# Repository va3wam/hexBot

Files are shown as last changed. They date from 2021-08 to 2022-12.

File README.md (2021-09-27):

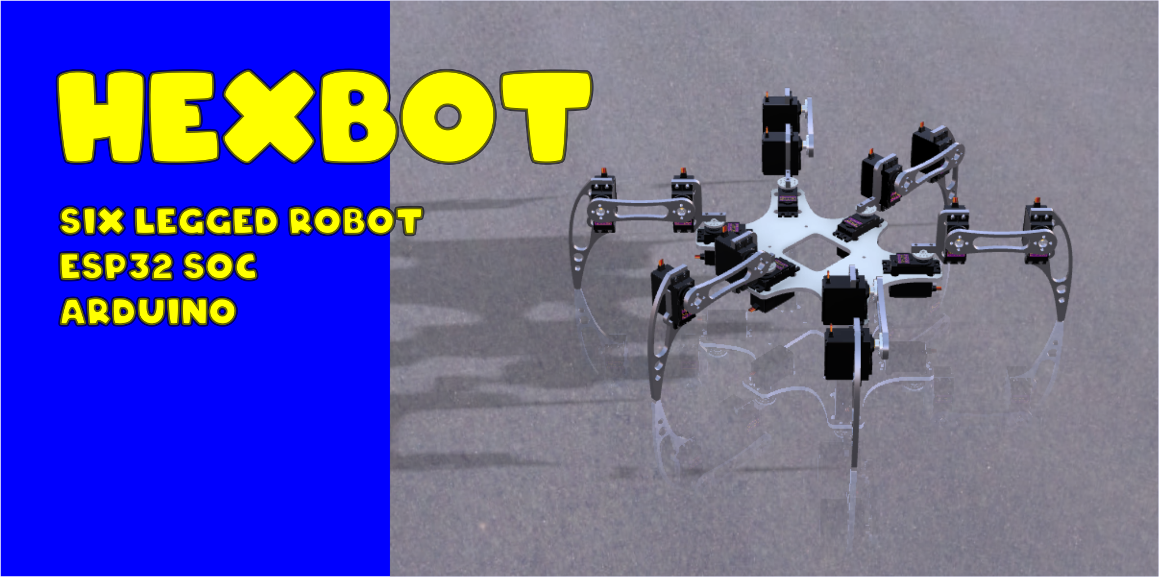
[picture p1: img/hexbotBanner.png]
hexaBot




This repository contains the Arduino source code that runs on an embedded processor at the heart of the six legged robot we call HexBot. The goals of this project can be found [here](goals.md). 

# Getting Started

This project requires that you have a Hexbot robot. The Robot is made up of a custom robot chassis and PCB as well as the code in this repository. Without a version 3 or later Hexbot robot this code will not be very useful to you. 

# Documentation

Here is an index of links to helpful documents found in this repository.

## Constructing a Hexbot Robot
* List of [hardware components](/docs/hexbotHardware.md).
* Hexbot [assembly instructions](/docs/hexbotAssembly.md).
* How to [wire the motors](/docs/wireMotors.md).

## Hexbot User Guides
* Hexbot's [Web interface](/docs/hexbotWebInterface.md).
* How to [configure NVRAM remotely](/docs/hexbotWebInterface.md#config-updater-screen).
* How to [perform OTA updates](/docs/hexbotWebInterface.md#ota-updater-screen).
* Available [MQTT commands](/docs/mqttCommands.md).
* [Hexbot Operations manual](/docs/hexbotOperationManual.md).

## Hexbot Developers Guide

### Prerequisites

In order to make use of the code in this repository you will require the following items.

* A Hexbot robot made up of [this hardware](/docs/hexbotHardware.md).
* The [Hexbot custom PCB](/docs/hexbotCircuit.md).
* An [MQTT broker](/docs/MQTTbroker.md) used by the robot's [MQTT web interface](/docs/hexbotWebInterface.md).  
* A [clone](/docs/cloneRepository.md) of the Hexbot gitHub repository into your own local Git repository.

### Development Software Stack

* How to [clone](/docs/cloneRepository.md) the Hexbot gitHub repository.
* Sample [platformio.ini](AA/platformIO-MAC-example.txt) template.
* Set up [PlatformIO](https://github.com/va3wam/hexBot/blob/main/docs/cloneRepository.md#set-up-platformio).
* Recommended Visual Studio Code [plugins](https://github.com/va3wam/hexBot/blob/main/docs/cloneRepository.md#visual-studio-code-plugins).

### Code Compatability

Hexbot software runs as a monolithic firmware image. The high level logic and peripheral interactions are handled using Arduino C++. FreeRTOS is used to run a WiFi stack as well as the primitive xTaskCreatePinnedToCore() which is used to manage mutli-threaded process execution.

Hexbot's firmware is intended to run on the Espressif ESP WROOM32 "Software On a Chip" (SOC). The development board used for this SOC is the [Zerynth DOIT Esp32 DevKit v1](https://testzdoc.zerynth.com/reference/boards/doit_esp32/docs/). ```We may be switching to a different board``` Note that some standard Arduino functions such as AnalogWrite() have not been implemented on the ESP32 SOC and alternate functions such as ledcSetup(), ledcAttachPin() and ledcWrite() must be used in their place. There are some additional compatability issues of note as follows:

* The GPIO pin usage is loosey Adafruit featherboard compliant meaning it will work with some boards such as the Adafruit OLED featherboard.
* This code will NOT run on an ESP8266 unmodified because of both GPIO incompatability as well as some ESP32 specific libraries that are in use.

### Installing

A set of instructions on how to install the source code for VA3WAM projects can be found [here](https://va3wam.github.io/versionControl/).

### Testing

At this time we have no tools or standards for automated testing of Arduino code on an embedded system. 

### Deployment

Use serial over USB to load the inital code onto the embedded system. Subsequent builds can be uploaded using either serial over USB or 
a [OTA web interface](/docs/webOTA.md) hosted by the robot which allows you to do [OTA](https://en.wikipedia.org/wiki/Over-the-air_programming) updates.

### Built With

* [Visual Studio Code](https://code.visualstudio.com/) - Text editor.
* [PlatformIO](https://platformio.org/) - IDE for ESP32 based Arduino development.

If you are new to these tools then you may want to read [this](https://randomnerdtutorials.com/vs-code-platformio-ide-esp32-esp8266-arduino/).

### Contributing

Please read [CONTRIBUTING.md](contributing.md) for details on our code
of conduct, and the process for submitting pull requests to us.

### Versioning

We use [Semantic Versioning](http://semver.org/) in naming the [releases](https://github.com/va3wam/hexaBot/releases) of this code base. 

# Kinematic Model

Hexbot uses an inverse kinematic model to manipulate it's legs. To learn more about our implementation of an inverse kinematic model look <a href="/docs/kinematicModel.md">here</a>.

# Authors

* **[Old Squire](https://github.com/theagingapprentice)**
* **[Doug Elliott](https://github.com/nerdoug)**

# License

This project is licensed under the [MIT License](license.md).

# Acknowledgments

* Robot chassis design inspired by [Cameron Buss' Swampy the Hexapod](https://grabcad.com/library/swampy-the-hexapod-1).
* 3 DOF Inverse Kinematic code inspired by [Avatar
Aymen Nacer](https://github.com/AymenNacer/Forward-and-Inverse-Kinematics-for-3-DOF-Robotic-arm). 
* Tony DiCola and Adafruit Industries for their MQTT QOS1 Arduino library.
* Jeff Rowberg for the MPU6050 DMP logic. ```May not use.```
* DFRobot & John Rickman for their LiquidCrystal I2C LCD display Arduino library. ```May not use.```
* The many folks involved in porting the Arduino libraries over to the ESP32.

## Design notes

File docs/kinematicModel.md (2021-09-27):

<h1>Kinematic Model</h1>

We use an inverse kinematic model to manipulate the legs of Hexbot. We are experimenting with this 
<a href="https://github.com/cgxeiji/CGx-InverseK">Arduno library</a> to see how effectively we can  
manipulate the robot's legs. Figure 1 shows how the cartesian coordinate system applies to the right leg of the Hexbot robot.

<figure>
  Model
  <figcaption>Fig.1 - Hexbot Right Leg.</figcaption>
</figure> 

<h1>Reference Material</h1> 
This 
<a href="https://www.mathworks.com/help/fuzzy/modeling-inverse-kinematics-in-a-robotic-arm.html">matlab article</a>
discusses a fuzzy logic approach to manipulating a leg.

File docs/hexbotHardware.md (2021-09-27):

# Hexbot Hardware

This page lists all the parts that you need in order to build your own Hexbot. 

## Chassis

Hexbot's chassis is comprised of a lower main body section with six protruding legs and a PCB mounted on top. The body and legs are milled out of 6061 extruded aluminium. When pully assembed Hexbot's physical dimensions are roughly:

* Height = ~ 5 inches when in neutral standing position.
* Length = ~ 14 inches when in neutral standing position.
* Weight = ~ 3 lbs 7.5 Oz without battery or PCB.

Hexbot's chassis is comprised of 1 lower body panel, 6 hip components, 6 upper leg components and 6 lower leg components. *Note that you will need to fabricate your own upper body component used for mounting the electronics*.   

<table>
  <tr>
    <td align ="left"> 
       <figure>
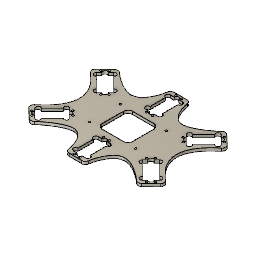
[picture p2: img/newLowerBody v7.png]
Main body
          
          <figcaption>Fig.1 - Main body</figcaption>
       </figure> 
    </td>
  </tr>
  <tr>
    <td align ="left"> 
       <figure>
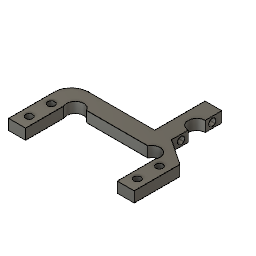
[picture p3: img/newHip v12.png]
Hip
          
          <figcaption>Fig.2 - Hip</figcaption>
       </figure> 
    </td>
  </tr>
  <tr>
    <td align ="left"> 
       <figure>
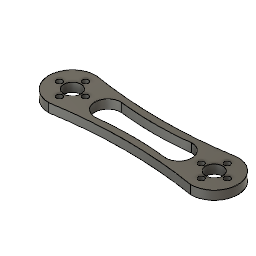
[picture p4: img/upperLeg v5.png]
Upper leg
          
          <figcaption>Fig.3 - Upper leg</figcaption>
       </figure> 
    </td>
  </tr>
  <tr>
    <td align ="left"> 
       <figure>
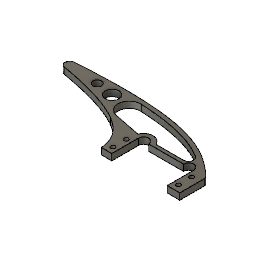
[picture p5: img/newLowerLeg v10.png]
Lower leg
          
          <figcaption>Fig.4 - Lower leg</figcaption>
       </figure> 
    </td>
  </tr>
</table>  

## Micellaneous Hardware

In addition to the parts above you will also need 

* 72 [M3 0.5 x 10 cap head screws](https://www.amazon.ca/gp/product/B07FDLN8C3/ref=ppx_yo_dt_b_asin_title_o01_s00?ie=UTF8&psc=1)
* 64 [M3 nuts](https://www.amazon.ca/gp/product/B07FDLN8C3/ref=ppx_yo_dt_b_asin_title_o01_s00?ie=UTF8&psc=1)
* 18 [Mallofusa 25 tooth Servo Horn](https://www.amazon.ca/Mallofusa-Servo-Aluminum-Silvery-Helicopter/dp/B00NOGMK3M). 
* 18 M3 0.5 x6 button head screws (come with the horns). 
 
## Motors

<table>
  <tr>
    <td align ="left"> 
       <figure>
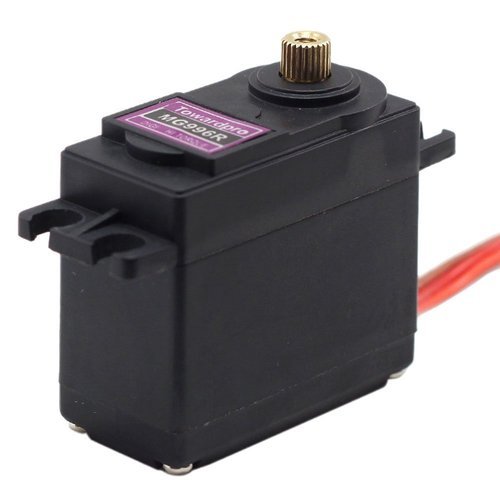
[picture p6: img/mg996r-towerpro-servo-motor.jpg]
servo motor
          
          <figcaption>Fig.5 - Servo motor</figcaption>
       </figure> 
    </td>
    <td align ="left"> 
       Hexbot has a total of 18 leg joints. These leg joints are 
       <a href="https://components101.com/motors/mg996r-servo-motor-datasheet">MG996R Servo motors</a>. The applied voltage of this motor should be in range of 4.8 to 7.2V. The frequency of motor is 50 Hz and the PWM duty cycle is 20 milliseconds. This motor has 3 pins as follows:
      <ul>
         <li>PWM: Orange</li>
         <li>VCC: Red</li>
         <li>GND: Brown</li>
      </ul>
    </td>   
  </tr>
</table>  

## Servo Horns

<table>
  <tr>
    <td align ="left"> 
       <figure>
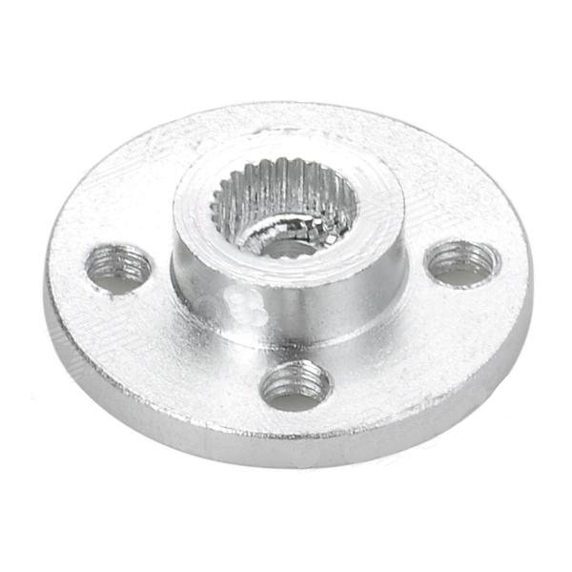
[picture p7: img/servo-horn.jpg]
servo horn
          
          <figcaption>Fig.6 - Servo horn</figcaption>
       </figure> 
    </td>
    <td align ="left"> 
       Each servo motor requires an 
       <a href="https://www.amazon.ca/gp/product/B00NOGMK3M/ref=ppx_yo_dt_b_asin_title_o04_s00?ie=UTF8&psc=1">aluminium round servo horn with a 25 tooth spline</a>. 
    </td>   
  </tr>
</table>  

## Motor Drivers

<table>
  <tr>
    <td align ="left"> 
       <figure>
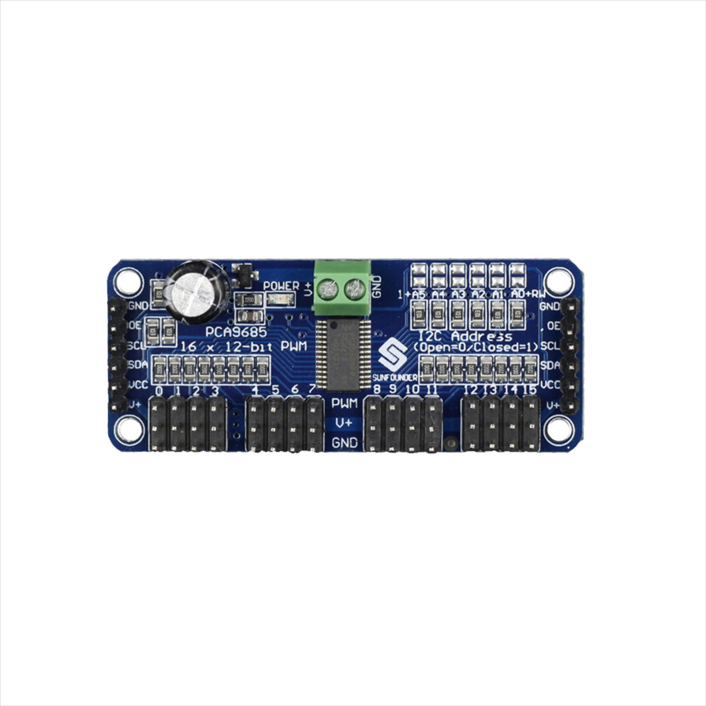
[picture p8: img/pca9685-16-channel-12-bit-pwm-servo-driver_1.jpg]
motor driver
          
          <figcaption>Fig.7 - Motor driver</figcaption>
       </figure> 
    </td>
    <td align ="left"> 
       The Hexpod robot requires a way to connect a large number of servo motors to a microcontroller with limit IO pins. To achieve this we use a pair of Adafruit <a href="https://cdn-learn.adafruit.com/downloads/pdf/16-channel-pwm-servo-driver.pdf">PCA9685 16-channel 12-bit servo motor drivers</a>. These motor drivers have their own onboard NXP Semiconductors <a href="http://www.adafruit.com/datasheets/PCA9685.pdf">PCA9685 microcontrollers</a> that handles the details of PWM signalling to the motors so all we have to do is communicate to them via I2C which only consumes 2 IO pins. The defult I2C address for the driver is 64 (0x40). There is also an all-call address at 112 (0x70). Since hexBot has 18 motors and a single driver can only handle a maximum of 16 we need to use 2 of these drivers. Since both drivers are on the same I2C bus we need to change the I2C address of the second driver to avoid conflicts. Page 13 of the Adafruit document explains how to do this.     
    </td>   
  </tr>
</table>  

## Line level converter

<table>
  <tr>
    <td align ="left"> 
       <figure>
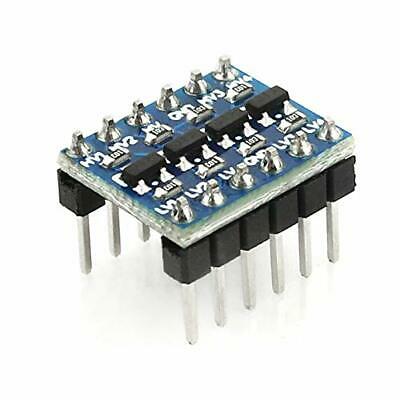
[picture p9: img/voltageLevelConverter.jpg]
          
          <figcaption>Fig.8 - I2C bus voltage converter</figcaption>
       </figure> 
    </td>
    <td align ="left"> 
       Since the ESP32 microprocessor used for Hexbot's brain is a 3.3VDC device and the PCA9685 microprocessor used in the motor driver board is a 5 VDC device we must use a line level converter on the I2C bus to connect between them. Hexbot uses the KeeYees <a href="https://www.amazon.ca/gp/product/B07LG646VS/ref=ppx_yo_dt_b_asin_title_o00_s00?ie=UTF8&psc=1">4 Channel I2C Logic Level Converter Bi-Directional Module</a> which appears to be a clone of the Sparkfun Bi-Directional Logic Level Converter. For wiring help check out the <a href="https://learn.sparkfun.com/tutorials/bi-directional-logic-level-converter-hookup-guide/all">wiring guide</a>. 
    </td>   
  </tr>
</table>  

## Main processor

<table>
  <tr>
    <td align ="left"> 
       <figure>
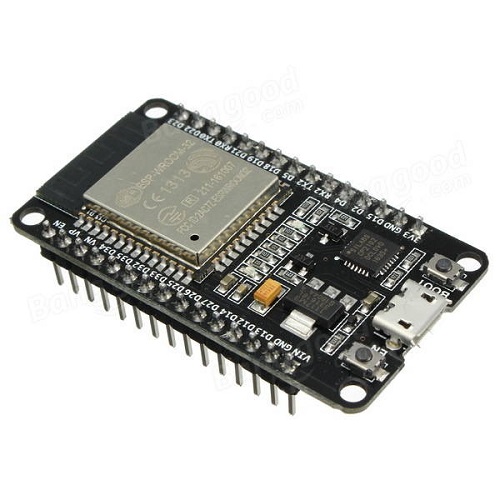
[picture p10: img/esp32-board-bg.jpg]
ESP32 dev board
          
          <figcaption>Fig.9 - ESP32 Dev Board</figcaption>
       </figure> 
    </td>
    <td align ="left"> 
       The brains of Hexbot come courtesy of an Espressif <a href="https://va3wam.github.io/soc/technology%20stack/architecture/SOC-Technology-Stack/">ESP32</a> Software On a Chip (SOC). We are using Zerynth's 30 pin variant of their <a href="https://testzdoc.zerynth.com/reference/boards/doit_esp32/docs/">DOIT Esp32 DevKit v1</a> development board for ESP32 integration into our circuit.  
    </td>   
  </tr>
</table>  

## Motion Sensors

```Not sure if we will use this or not```

The robot’s motion tracking is provided by an Invensense MPU6050 inertial measurement unit development board which combine a 3-axis 
microelectromechanical gyroscope and a 3-axis accelerometer on the same silicon die, together with an onboard Digital Motion Processor (DMP), which processes complex 6-axis MotionFusion algorithms. 

## Power Management

The robot is powered by direct current provided by a Dewalt 20V 3AH lithium-ion battery. This voltage is stepped down to a 12 volt bus, a 5 
volt bus and a 3.3 volt bus using a Drok LM2596 multiple output power supply.  

## Buttons

The robot features a [reset and selection button](https://www.adafruit.com/product/3350) as well as a [power button](https://www.adafruit.com/product/4659). These buttons feature embedded software controlled LEDs that allow for the robot to give visual queues as to what it is doing.

## OLED/LCD

```Not sure what display we will use yet```.

## Assembly
Full step by step instructions for Hexbot can be found [here](hexbotAssembly.md).

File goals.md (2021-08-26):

# Project Goals

This repository contains the code and documentation that supports the **Hexapod Robot** project. The goals of this project are as follows.

## Functional Goals

* Stand and return to resting position - _Incomplete_
* Coordinated individual leg movement  - _Incomplete_
* Coordinated multiple leg movement - _Incomplete_
* Multiple walking gates - _Incomplete_
  
## Software Goals

* Understand the Arduino inverse kinematic library - _Incomplete_
* Develop a custom inverse kinematic algorithm - _Incomplete_
* Break code into function include files - _Incomplete_
* Settle on a new set of coding standards - _Incomplete_

## Hardware Goals

* Learn to machine aluminium - _Complete_
* Learn to make two sided PCBs - _Incomplete_

## Github/Dev Process Goals

* Learn to use Git to recall past code commits - _Incomplete_
* Learn to use releases in GitHub - _Incomplete_

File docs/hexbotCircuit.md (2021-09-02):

# PCB

This page has details about the PCB used for the Hexbot robot. At present we are using a breadboard because we have not designed or manufactured the PCB. Here are the details regarding the breadboard.  

## Design

The circuitry for the Hexbot robot is designed in Eagle CAD.

## Fabrication

The PCB is fabricated using a third party service. 

## Design

The circuitry for the Hexbot robot is designed in Eagle CAD.

## Fabrication

The PCB is fabricated using a third party service. 

## Breadboard wiring

<table>
   <caption>Dev Board Pinout Diagram</caption>
   <tr>
      <td align ="left"> 
         <figure>
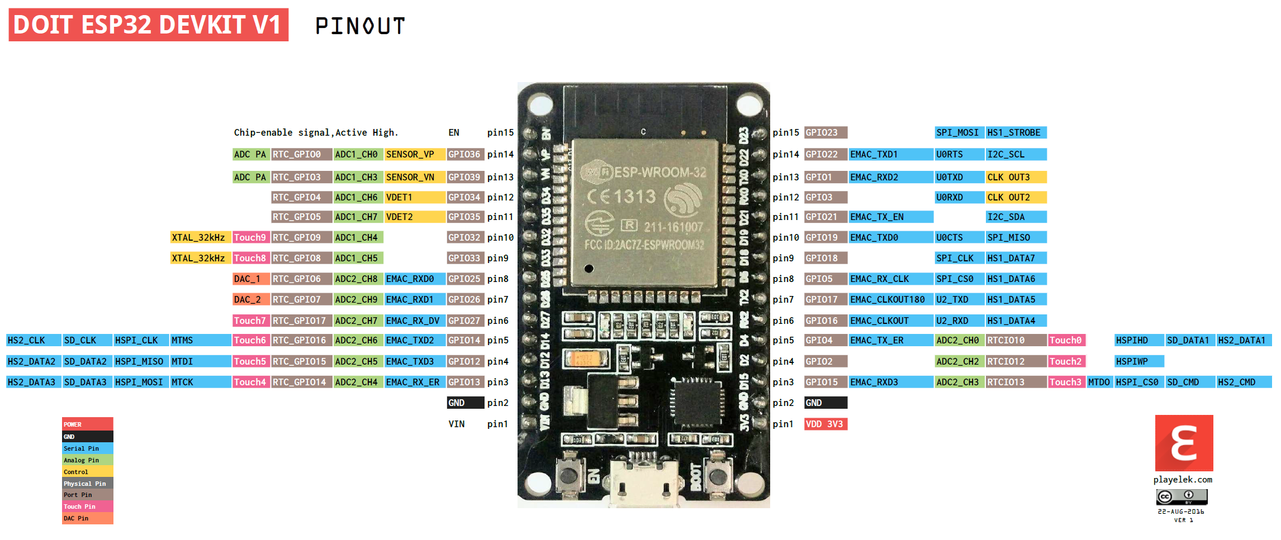
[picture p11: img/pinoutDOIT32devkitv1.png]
Dev board pinout
            <br>
            <figcaption>Fig.1 - Dev board pinout.</figcaption>
         </figure> 
      </td>
   </tr>
   <tr>
      <td>
         <code>
         Note that for some silly reason this diagram uses the same numbers on the left and right so to differentiate them we put an L for left and R for right infront of the physical pin numbers.
         </code>
      </td>
   </tr>
   <tr>
      <td align ="left"> 
         <table>
            <caption>Dev Board Pin Usage</caption>
            <tr>
               <th>Label</th>
               <th>Physical</th>
               <th>GPIO</th>
               <th>Use</th>
            </tr>
            <tr>
               <td>D21</td>
               <td>R11</td>
               <td>21</td>
               <td>I2C SDA</td>
            </tr>
            <tr>
               <td>D22</td>
               <td>R14</td>
               <td>22</td>
               <td>I2C SCL</td>
            </tr>
            <tr>
               <td>D14</td>
               <td>L5</td>
               <td>14</td>
               <td>Monitor right motor driver PMW freq.</td>
            </tr>
            <tr>
               <td>D12</td>
               <td>L4</td>
               <td>12</td>
               <td>Monitor left motor driver PMW freq.</td>
            </tr>
         </table>
      </td>
  </tr> 
  <tr>
     <td>
         <table>
            <caption>Breadboard Fritzing Diagram</caption>
            <tr>
               <td align ="center">     
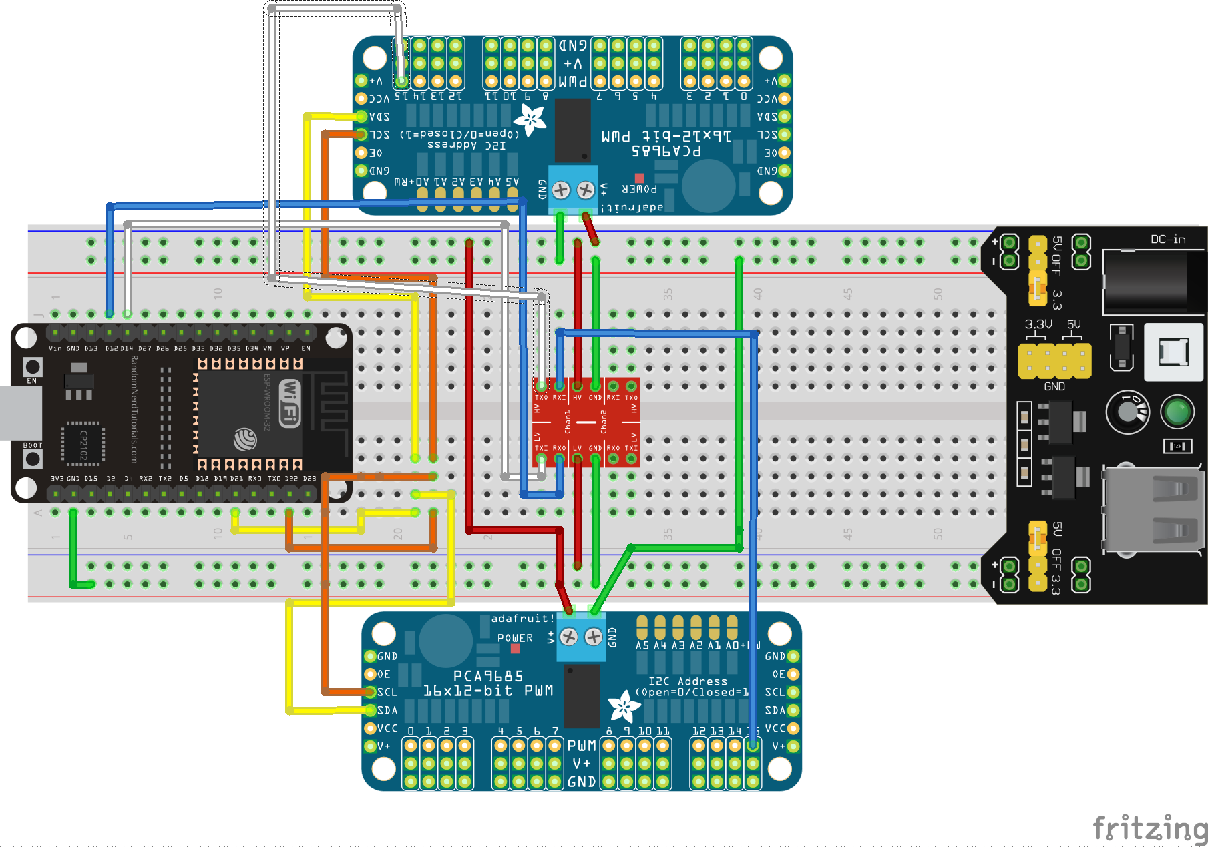
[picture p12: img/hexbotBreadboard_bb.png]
Breadboard
                  <br>
                  <figcaption>Fig.2 - Breadboard.</figcaption>
               </td>
            </tr>
        </table>
     </td>
   </tr>
</table>

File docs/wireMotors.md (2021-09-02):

# Wiring Motors

There are 18 motors that need to be connected to 2 different motor drivers. The purpose of this document is to ensure that your Hexbot's motor wiring is done the same way that the code in this repository expects it to be.

 <figure>
  Motor wiring
  <figcaption>Fig.1 - Hexbot servo motor wiring reference.</figcaption>
</figure> 

## Wiring Chart

Please refer to figure 1 to understand the references made in this chart. Once you have the motors set up you will need to sort out the <a href="/docs/hexbotCircuit.md">circuitry</a>.

<table>
   <tr>
      <th>Left Side</th>
      <th>Right Side</th>
   </tr> 
   <tr>
      <td>
         <table>
            <tr>
               <th align="center">Leg</th>
               <th align="center">Motor</th>
               <th align="center">Driver 1 Port</th>
            </tr>
            <tr>
               <th rowspan="3">L1</th>
               <th align="center">H1</th>
               <td align="center">0</td>
             </tr>
             <tr>
                <th align="center">K1</th>
                <td align="center">1</td>
             </tr>
             <tr>
                <th align="center">A1</th>
                <td align="center">2</td>
             </tr>
             <tr>
               <th rowspan="3">L2</th>
               <th align="center">H2</th>
               <td align="center">3</td>
             </tr>
             <tr>
                <th align="center">K2</th>
                <td align="center">4</td>
             </tr>
             <tr>
                <th align="center">A2</th>
                <td align="center">5</td>
             </tr>
             <tr>
               <th rowspan="3">L3</th>
               <th align="center">H3</th>
               <td align="center">6</td>
             </tr>
             <tr>
                <th align="center">K3</th>
                <td align="center">7</td>
             </tr>
             <tr>
                <th align="center">A3</th>
                <td align="center">8</td>
             </tr>
         </table> 
      </td> 
      <td>  
         <table>
            <tr>
               <th align="center">Leg</th>
               <th align="center">Motor</th>
               <th align="center">Driver 2 Port</th>
            </tr>
            <tr>
               <th rowspan="3">L4</th>
               <th align="center">H4</th>
               <td align="center">0</td>
             </tr>
             <tr>
                <th align="center">K4</th>
                <td align="center">1</td>
             </tr>
             <tr>
                <th align="center">A4</th>
                <td align="center">2</td>
             </tr>
             <tr>
               <th rowspan="3">L5</th>
               <th align="center">H5</th>
               <td align="center">3</td>
             </tr>
             <tr>
                <th align="center">K5</th>
                <td align="center">4</td>
             </tr>
             <tr>
                <th align="center">A5</th>
                <td align="center">5</td>
             </tr>
             <tr>
               <th rowspan="3">L6</th>
               <th align="center">H6</th>
               <td align="center">6</td>
             </tr>
             <tr>
                <th align="center">K6</th>
                <td align="center">7</td>
             </tr>
             <tr>
                <th align="center">A6</th>
                <td align="center">8</td>
             </tr>
         </table>        
      </td>
   </tr>
</table>

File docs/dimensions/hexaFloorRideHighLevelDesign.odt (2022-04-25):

# HexaFloorRide high level design

This document explains how the dimensions used for the HexaFloorRide robot were derived.

## Design philosophy

The design philosophy behind the new HexaFloorRide robot chassis is simply to preserve the cartesian coordinate system dimensions used to calculate the robot’s toe position as much as possible. That said a few fundamental things are different with this new design.

## Differences in the new design

The first difference between the old and new design plans are in metric not imperial units. In some cases this may slightly change dimensions resulting from rounding measurement. The reason for this change is two fold. First, using metric aligns the units that are used to design the chassis with the units used to calculate toe position. Second, metric units are favoured by the OEM data sheets for most of the components that make up the robot, including the servo motors. This change makes the units through out the entire design process for the robot consistent.

The second difference between the old and new design is that we have moved the toe from being outside of the ankle joint in the neutral position to being directly under the ankle joint when in the neutral position. This will change the trigonometry of the leg movements but only affects the toe offset term of the equation from its current value of 3.245 to 0 (defined as toeOffset in the flows.h file). The reason for this change is change is to reduce the torque demands of the ankle servo, which testing shows improves when this change in geometry is made.

The third difference between the old and new design is that we have switched from using generic MG996R hobby servo motors to HiTec HS-485HB hobby servo motors. These motors have slightly different physical dimensions. The reason for this change is to improve the precision of movement and too reduce the rate of failure of the motors. The new motors are also three times the cost (up front) but may end up cheaper in the long run if the failure rate of motors improves.

The fourth difference between the old and new design is that we have switched from using 1/4” to 3.175mm (1/8”) 6061 aluminum. The reason for this change is to reduce the weight of the robot to require less torque from the motors.

The fifth and final difference is that the old design used direct modelling and the new design uses parametric modelling. Time will tell if this change is for the better as both approaches have pros and cons.

## The robot’s anatomy

To describe the different parts of the HexaFloorRide robot we use the following anatomical terms:

1. The body. This is the main chassis of the robot. Please refer to figure 1.
2. The hip. This is the servo that connects to the thigh to the body.
3. The thigh connects to the horn of the hip servo as well as to the body of the knee servo.
4. The knee servo connects the thigh to the shin.
5. The shin connect the horn of the thigh servo to the horn of the ankle servo.
6. The ankle servo connect the shin to the foot.
7. The foot ends at the toe which is the primary reference point used to calculate servo angles for the robot’s leg movements.

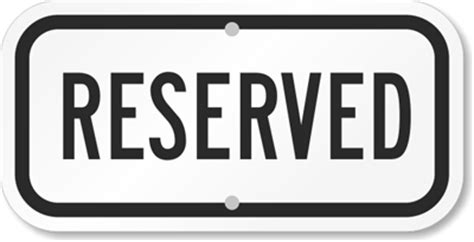
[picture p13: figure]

Figure 1: Leg terminology - picture TBD

## The robot’s joints

The robot has three joints on each of its six legs for a total of 18 joint. The joints on each leg are the hip, knee and ankle. Each joint is a Hitech HS-485B hobby servo motor (shown in Figure 2).

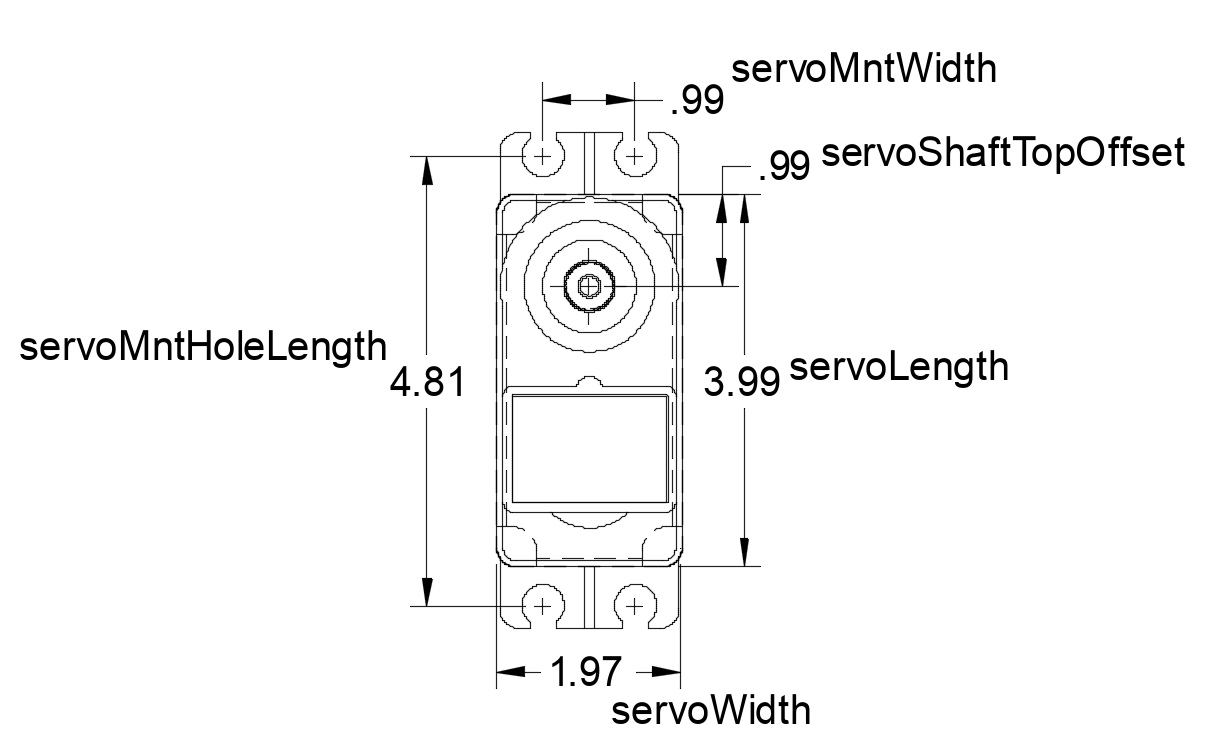
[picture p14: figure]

Figure 2: Hitech HS-485HB servo motor dimensions

Each joint also uses an aluminium horn that has a 24 tooth spline and an SES V1 mounting pattern (shown in figure 3). The key parameters are listed below.

1. hornCenterHole is the diameter of the centre hole that the mounting screw passes through to affix the horn to the servo shaft which equals 0.8cm.
2. hornMntGuideDiam is the diameter of guidance circle used to place four equally spaced holes around the horn. These holes are used for mounting the robot’s leg parts to the joints. This circle has a diameter of 1.66624 cm (0.656”).
3. hornThreadHoles s the drill hole size to accommodate threading a #2-56 screw which equals 0.86” (3/32”) or 0.238125 cm.
4. hornOuterDiam is the outer diameter of the horn which is 2.54 cm (1”).
5. hornSplineGreaterDiam is the grater diameter of the 24T spline used to mount onto the servo shaft which is 0.56 cm.
6. hornScrewHole is the drill hole size to accommodate passing a #2-56 screw without engaging the threads. This diameter is 0.238125 cm hole that can be drilled with a 3/32” drill bit.

See Figure 5. You can read about the different variations of the SES specification here: https://wiki.lynxmotion.com/info/wiki/lynxmotion/view/servo-erector-set-robots-kits/servo-erector-set-system-info/ses-mounting-pattern-information/

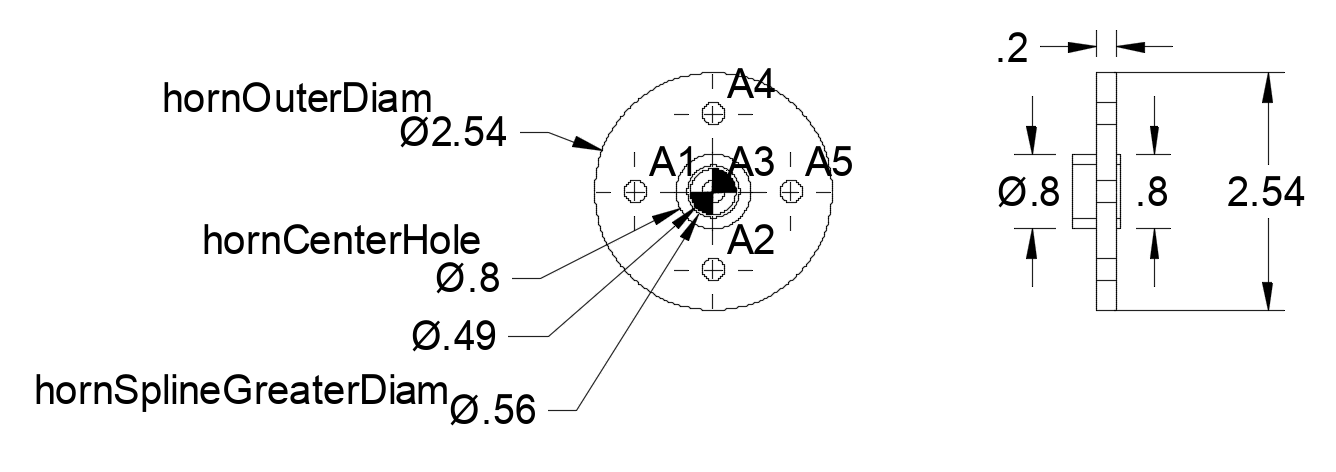
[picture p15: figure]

Figure 3: Servo horn dimensions.

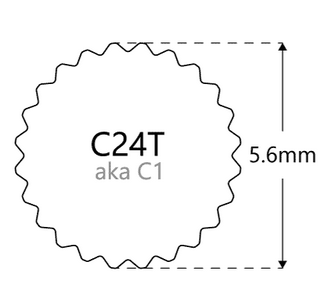
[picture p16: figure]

Figure 4: HiTec 24T spline

## The robot’s foot

The key parameters used for the design of the foot are listed below.

1. clearanceTolerance is the gap allowance used to ensure that parts such as the servo motors fit inside the spaces in the robot chassis created for them to fit inside. The formula used to calculate the clearance tolerance is material thickness (3.175) * die punch material factor for aluminium (0.15) which equals 0.4763 cm. This calculation came from the web site https://www.unipunch.com/support/calculators/die-clearance-calculator/.
2. servoShaftTopOffset is the distance from the flat top of the ankle servo’s main chassis to the shaft of the ankle servo that acts as the centre of rotation for the robot’s foot which equals 9.82 cm. (see figure 1)
3. ankleToToeDistance is the distance from the centre of the ankle servo shaft to the tip of the toe on the foot which equals 11.059 cm defined as footLength in the flows.h file. (see figure 5)
4. servoLength is the length of the main part of the servo motor chassis that seats inside the foot. This is calculated as the published dimension for the length of the servo motor which equals 3.99 cm. (see figure 1)
5. servoWidth is the width of the main part of the servo motor chassis that seats inside the foot which equals 1.97 cm. (see figure 1)
6. servoMntHoleLength is the distance lengthwise between the two sets of mounting holes for the servo motor which equals 4.81 cm. (see figure 1)
7. servoMntWidth is the distance widthwise between the mounting holes on one end of the servo motor which equals 0.99 cm. (see figure 1)
8. servoMntHoleDiam is the drill hole size to accommodate threading a #2-56 screw which equals 0.86” (3/32”) or 0.238125 cm.
9. shoeHole is the drill hole size to accommodate passing a #2-56 screw without engaging the threads. This diameter is 0.238125 cm hole that can be drilled with a 3/32” drill bit.
10. shoeOffset is the thickness of the shoe on the foot which equals 0.3175 cm. (see figure 5)
11. thickness defines both the minimum material thickness around cavities as well as defining how thick the material used to make the part is. This value is 0.3175 cm (1/8”).

Figure 5: foot dimensions. 1 = foot, 2 = shoe.

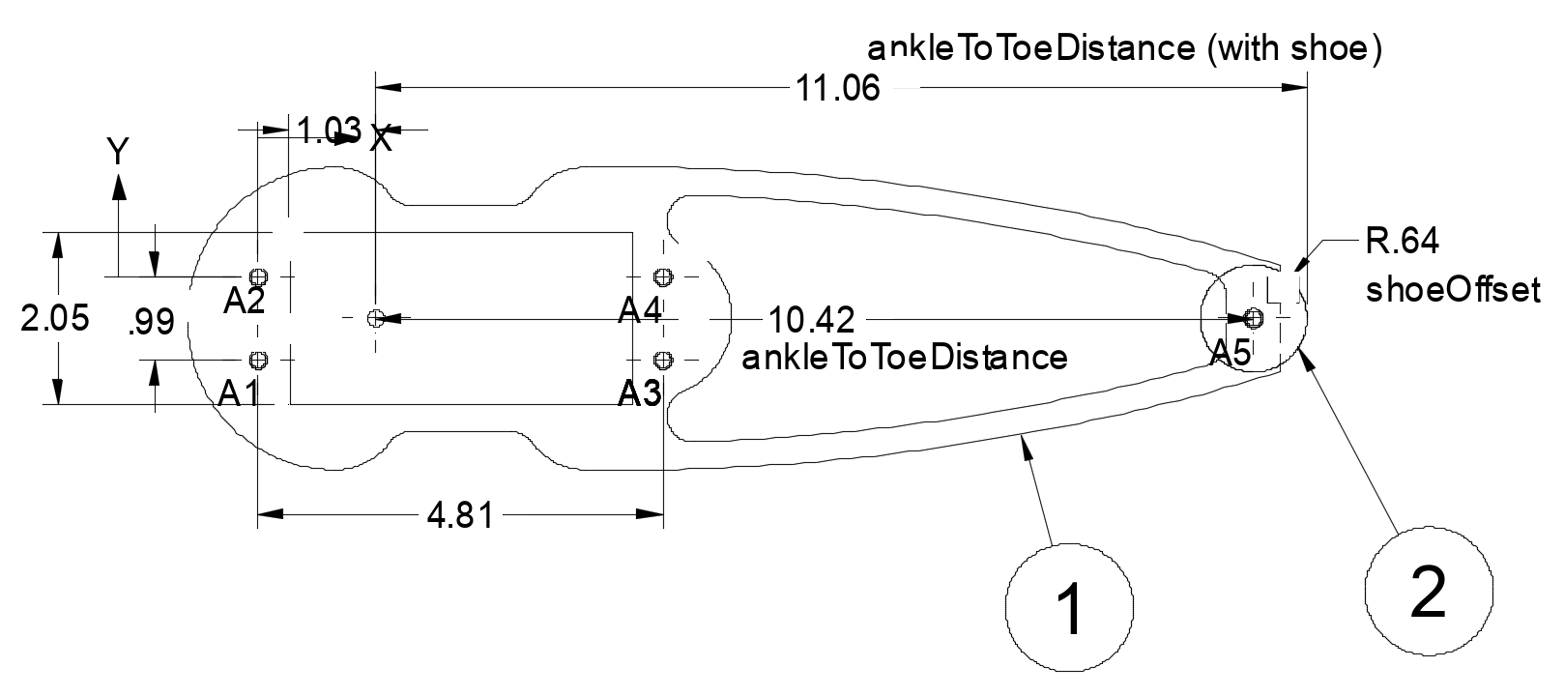
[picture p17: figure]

## The robot’s shoe

With this new design we will be able to experiment with different “shoes” that can be made of (or coated with) different materials. The shoe is a simple disk with a radius of 0.64 cm and a 3/32” canter hole that ill allow a #2-56 screw to pass through and screw into the foot at the toe. You can see the shoe placement in figure 5.

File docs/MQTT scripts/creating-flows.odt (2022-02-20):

## Creating and Troubleshooting Flows

### Introduction

Flows are text files that control movement of the legs on the Hexbot robot, and thus the movement of the robot itself. They are written in the javascript-like scripting language of the MQTT.fx utility that communicates with the robot using the MQTT protocol over Wifi.

The goal is to give minimum information to have Hexbot move toes on 6 legs in parallel from one position to the next, repeatedly in an overall sequence.

Flows can be created by hand, using a simple text editor like Notepad++ to enter them. Since 18 numbers are needed to specify toe movements, this is somewhat tedious. In some cases, it’s helpful to use a spreadsheet to create some of the numeric coordinates, export it to CSV format, and then transplant the calculated numbers into a flow.

Flow files have the .js file extension. Email programs typically don’t allow attachments with the .js extension, so if they’re renamed to .txt files temporarily for emailing purposes.

All coordinates and distances in this document are expressed in centimeters, and 2 decimal places of accuracy is sufficient, considering the resolution of our servos..

A project is under way to create a compiler that will allow creation of flow files using high level commands. This will be simpler, less labour intensive and more reliable. The troubleshooting section of this document may still be useful when the robot’s behaviour doesn’t match expectations.

### Coordinates and Movement

As implied by the name, the Hexbot has 6 legs, each of which contains 3 servo motors. The hip servo is mounted on the chassis. The knee servo is the next one outward, and the ankle is the last one. The link from the hip to the knee is called the thigh, and from the knee to the ankle is called the shin. The endpoint of the leg is called the toe, and the link between it and the ankle servo is called the foot.

Moving the robot is done in steps, each of which includes moving each leg at the same time to a new position. There are two main ways of specifying a toe position: global coordinates, and local coordinates.

Global coordinates are relative to the chassis of the robot. The +X direction is towards the front, the +Y direction is towards the robot’s left side, and the +Z direction is upwards. The global origin is at the geometric center of the chassis, at the same height as the rotation center of the middle servo (“knee”).

Local coordinates are relative to each leg, and all 6 legs are oriented differently. The local coordinate system is about to undergo a naming change, but for now, these axis names apply. The +X direction is straight out from the hip servo, the +Y direction is upwards, and the +Z direction is perpendicular to both X and Y axes, with positive being to the left when looking in the +X direction. Note that because of the way the servos are mounted, the +Z direction points towards the front on the Hexbot’s the right side, but towards the back on the left side.

To specify a step that is part of leg movement, you need to specify the new location for each of the 6 toes. These each need 3 coordinates, so this requires 18 numbers. There are several ways to give these coordinates, and you can use which ever one is convenient:

1. global coordinates for each toe. (Operations starting with MG...)
2. local coordinates for each toe. (Operations starting with ML...)

You can also give positions as an offset from the home, or neutral position. The home position occurs when all the servos are at their center position. The local coordinates for the home position are (13.78, -10.60, 0) for all 6 legs. You can specify offsets from the home position as follows:

1. offsets from the global coordinates of the home position, using global coordinate offsets. In this case, the 3 numbers refer to the global X,Y and Z directions. Operation MGRH = Move Global Relative to Home
2. offsets from the local coordinates of the home position, using local coordinate offsets. In this case, the 3 numbers refer to the local X, Y and Z directions. Operation MLRH = Move Local Relative to Home)

In a similar fashion there are also commands to move, using either global or local coordinate offsets, relative to the last position of the toe (i.e. the current position). These operations are: MGRL (Move Global Relative to Last) and MLRL (Move Local Relative to Last)

To simplify the process of specifying toe movements in some circumstances, there are commands that allow you to temporarily redefine where the home position is for each leg. Move commands that are relative to the home position will now be relative to the redefined position. The home position can be redefined as the current position of the toes, absolute toe locations using either global or local coordinates, or the original toe position when the hexbot is in the neutral stance. The associated operations are NHGC (New Home using Global Coordinates), NHLC (New Home using Local Coordinates), NHH (New Home Here), and NHR (New Home Reset).

### Timing and Frames

It might seem that the process of moving one leg’s toe to its position in the next flow would require just 3 servo movements, one for each servo in the leg. However, it’s a bit more complicated. There are a number of intermediary points that the servos move to, for 2 reasons:

- We want to control the speed of the movement
- We want the path of the toe to be a good approximation of a straight line.

These intermediary locations are referred to as frames. The number of frames for a movement varies, and is determined by 2 things:

1. The amount of time allowed for each frame movement. This is equivalent to the the desired frame rate, such as 24 frames per second. The default value for the frame time, f_msecPerFrame, is 50 milleseconds, which can be overridden in the DO_FLOW command of a script. DO_FLOW, toeMoveAction, 50 This corresponds to a frequency of 20 frames per second, which has proven to be a practical value.
2. The total time specified in the FLOW command for the toe movement. This is the first number in the FLOW command, and it’s expressed in milliseconds. A movement taking one second would have the value 1000 for this field. FL, 1000, 3, 10, 0, 0, 0, 0,0,0, 0,0,0, 0,0,0, 0,0,0, 0,0,0, 0,0,0

The number of frames for a movement (f_framesPerPosn) is the total time for the movement, divided by the time specified for each frame. In the examples above, the number of frames would be 1000 / 50 = 20, because that is the number that will fit into the allotted time.

The debug features that display and graph information for each toe position work on a frame by frame basis. This is why a particular flow row number will appear multiple times is these displays – you’re seeing data for each frame, and there are usually multiple frames for the movement described by one FLOW command.

### High Level Flow Execution Process

The steps to create movement of the robot are below. Each of these will be expanded in the following sections.

1. Break the desired robot movement down into sections, and make a rough plan for each section.
2. Create flow commands to implement each section. (Due to use of open loop servo motors that don’t provide feedback on current position, we start in the dark, not knowing where the toes are.)
3. Wrap the MQTT.fx script syntax around your flow commands. This is easily done by modifying a previously working script to use your commands, and other parameters.
4. Prepare for testing without actually moving the servos by adjusting the final DO_FLOW command’s first parameter, which can also be used to enable some debugging outputs. You can also disable leg movement by turning off the 5 volt power to the PWM boards.
5. Use the MQTT.fx script command to load the flow into the Hexbot and execute it.
6. Check for toe safety violations on the console, which will halt execution of the script.
7. Optionally create a graph of the toe movements, and verify they’re what you expect.
8. Enable actual leg movement by adjusting the DO_FLOW toeMoveAction parameter and/or turning on 5 volt power to the PWM boards. Reload, and execute the flow.
9. Troubleshoot any unexpected behaviours
10. Document the script

### Movement Breakdown

Dividing a script into smaller pieces simplifies the creation effort, and debugging. When the movement consists of a gait with 2 phases, it makes sense to do each phase as a section. As well, if a portion of the script will be repeated, possibly using the cycle commands, treat it as one section. If you’re using a spreadsheet to generate the numbers needed, it’s helpful to treat that as one section.

Techniques that help you work with sections are:

- use comments starting with // in the script as descriptive separators between sections. After a while, all FLOW commands look the same, and this will help you navigate.
- use /* ... */ style comments to remove other following sections for testing. This helps you zero in on the last movements
- use the formatted flow dump to examine the related flow commands, especially if shorter cycle commands bracket the section you’re working on
- in the Calc graph of toe positions, hide rows for other sections to declutter the graph so it shows only your section. You can also unhide one flow row at a time to see if the resulting toe positions match your expectations. Note that the flow row number is the first number in each line of the Calc data, as well as in the formatted flow dump.

### Creating Basic Flow Commands

A flow script consists of 3 parts:

1. The initial NEW_FLOW command
2. Multiple FLOW commands forming the body of the flow
3. The final DO_FLOW command.

#### Initial NEW_FLOW

The first command send to the Hexbot in a script must be:

NEW_FLOW

which can be abbreviated to

NF

Flow command names are case insensitive, and lower case can be used. This command effectively clears out any previously defined flow, and does initialization for a new one.

#### FLOW Commands

The FLOW command (short forms FL or fl) is the most frequently used command in a flow. It has a long form for leg movements, and short form for cycle control commands.

Num-code | Op-code | Size | Meaning | Description
1 | MGC | long | Move to Global Coordinates | move to location specified by global coordinates in FLOW command
2 | MLC | long | Move to Local Coordinates | move to location specified by local coordinates in FLOW command
3 | MGRH | long | Move, Global offsets Relative to Home | move to a location which is offset from home position by the GLOBAL deltas in the FLOW command
4 | MLRH | long | Move, Global offsets Relative to Home | move to a location which is offset from home position by the LOCAL deltas in the FLOW command
5 | MGRL | long | Move, Global offsets Relative to Last | move to a location that’s offset from the last (current) toe position by the GLOBAL deltas in the FLOW command
6 | MLRL | long | Move, Local offsets Relative to Last | move to a location which is offset from the last (current) toe position by the LOCAL deltas in the FLOW command
20 | NHGC | long | New Home, Global Coordinates | Redefine the Home positions for each toe to be the GLOBAL coordinates in the FLOW command
21 | NHLC | long | New Home, Local Coordinates | Redefine the Home positions for each toe to be the LOCAL coordinates in the FLOW command
41 | NHH | Short | New Home Here | Redefine the Home positions for each toe to be their current locations
42 | NHR | Short | New Home Reset | Redefine the Home positions for each toe to be their original location where all servos are centered
43 | CPF | Short | Continue Previous Flow | Continue from the previous flow command, and don’t jump directly to location in first flow row.
50 | MCS | Short | Mark Cycle Start | Define the starting point of a repeatable named cycle to be the next flow row.
51 | MCE | Short | Mark Cycle End | Define the end point of a repeatable named cycle to be the previous flow row.
52 | DC | Short | Do Cycle | Execute a named cycle for a specified number of iterations
60 | TSX | Short | Toe Safety X limits | Redefine the allowable toe displacements from home in the positive and negative X directions
61 | TSY | Short | Toe Safety Y limits | Redefine the allowable toe displacements from home in the positive and negative Y directions
62 | TSZ | Short | Toe Safety Z limits | Redefine the allowable toe displacements from home in the positive and negative Z directions
63 | TSR | Short | Toe Safety Reset | Redefine the allowable toe displacements to be the default values defined at compilation time

(operations that are greyed out have not been implemented yet)

#### Long Form FLOW Command – Leg Movement

The long form FLOW command has these fields, separated by commas:

1. command name: FLOW, or FL
2. f_msecs: time duration for this leg movement (except for first flow command)
3. f_operation: The kind of action to be taken and interpretation of the numeric arguments for each leg. See the table above. Can be specified as an ALPHA mnemonic as shown in the above table, or a numeric code.
4. f_lShape1: (currently we only support straight lines, value 10, between toe positions) fl_straight = 10; // straight line fl_parabola = 11; // parabola fl_ellipse = 12; // ellipse, (including circle)
5. f_lShape2: currently unused and always 0 in long FLOW commands
6. f_lShape3: currently unused and always 0 in long FLOW commands
7. f_lShape4: currently unused and always 0 in long FLOW commands
8. Leg 1’s X value, with a meaning determined by f_operation field above
9. Leg 1’s Y value
10. Leg 1’s Z value
11. Leg 2’s X value . . .

25. Leg 6’s Z value

example: FL, 500, MLRH, 10, 0, 0, 0, 0,0,0, 0,0,0, 0,0,0, 0,0,0, 0,0,0, 0,0,0
would move all legs to their home positions in half a second.

#### Short Form FLOW Commands – Cycles & Toe Safety

Short form FLOW commands perform some sort of control function rather than an explicit leg movement that requires 18 numbers to control it. These commands are used for:

1. repeating sections of a script, referred to as cycles
2. modifying the toe safety check parameters on the fly
3. redefining the home position to simplify leg movement math
4. smoothing the transition between 2 consecutive flow executions

##### Repeating Parts of a Script

Because it is expected that subsets of a flow may be repeated, there are FLOW commands with special f_operation values to do the following:

1. Mark the beginning of a section of the flow that will be repeated later, and give the section a name. Sections, or cycles, have numeric integer names from 0 to 10.  Operation code: Mark Cycle Start, code MCS, or 9 Example: FL, 0, MCS, n, 0, 0, 0 where n is a numeric name assigned to the section
2. Mark the end of a repeatable section.  Operation code: Mark Cycle End, code MCE or 10 Example: FL, 0, MCE, n, 0, 0, 0 where n is a numeric name assigned to the section
3. Request the execution of a named section for a specified number of repetitions  Operation code: Do Cycle, code DC or 11 Example: FL, 0, DC, n, r, 0, 0 where n is the cycle name, r is repetition count

Sections must be defined before they can be requested for execution.

##### Updating Toe Safety Parameters

To prevent errors in coding FLOW commands from causing damage to the Hexbot, and burning out servo motors in particular, a safety check is done before any toe movement. The calculated position is to see how far it is from the home position on each of the local coordinate axes. (This home position is not affected by the FLOW commands NHGC, NHLC, NHH and NHR). There is limit specified for both the positive and negative directions for each axis. Default values, expressed in centimeters, are included at compile time as the parameters:

expect to add another short command that allows dynamic definition of the 6 toe safety check parameters. Unfortunately, it needs more numeric arguments than are available in the short FLOW command, so we need a different command:

SAFETY_BOX, XP, XN, YP, YN, ZP, ZN

See issue 134 for details.)

#### Final DO_FLOW Command

The last command sent to the Hexbot in a flow must be a DO_FLOW command that ends the definition of the flow, and starts its execution. It has the form:

DO_FLOW, toeMoveAction, msecPerFrame
where:

toeMoveAction

Is a bit encoded instruction on what to do when the next position (i.e. frame) for the toes has been calculated:

1 – move the servos so the toes actually move to the calculated position.
This is often disabled during testing. A functional equivalent not
needing an edit of the MQTT script is removing the 5 volt power
to the PWM boards
2 – display the angles for each of the 18 servos. See note below

4 – display the calculated PWM values for each servo. See note below

8 – display the local coordinates of the toe positions

16 – display the toe positions using global coordinates in a format suitable

for pasting to Calc to generate a graph of successive toe positions

32 – Before executing the flow, display it in a conveniently formatted
layout with aligned columns and flow row numbers on the left
msecPerFrame | is the value in milliseconds for f_msecPerFrame, which defines the resolution of intermediary toe movements along the line between its positions in consecutive FLOW commands. The standard value is 50 msec., which equates to 20 frames per second. Can be omitted – takes default

NOTES:

1. Only one of toe-actions 2, 4, 8, or 16 should be enabled at a time to avoid corrupted output
2. The legs are processed in an order that alternates between PWM boards to ease the burst load on those boards. The leg order is: 1, 4, 2, 5, 3, 6 . The debug displays show the data for the legs in the same order, i.e. L1X, L1Y, L1Z, L4X, L4Y, L4Z, L2X, L2Y ...
3. This unusual ordering of the leg data doesn’t affect the Calc graph, because it’s doing a scatter graph, and puts the position marker in the right location regardless of the order in which they appear.

### Putting Flow Commands into a Script

The NEW_FLOW, FLOW and DO_FLOW commands make up most of a downloadable MQTT.fx script, but there are other elements that are needed. Here’s a list of all the recommended parts of a script:

1. File format identifier: var Thread = Java.type("java.lang.Thread");
2. The execute call that encapsulates the script: function execute() {
3. An optional command to display the name of the script to the MQTT.fx download window: out("hexbot-walk.js");
4. Identification of the MQTT topic to send commands to: myTWIPe = "Hexbot3C61054ADD98/commands" // Doug's bot
5. The initial NEW_FLOW command that starts the script send("NEW_FLOW") // clear any previous flow
6. The long and short FLOW commands making up the bulk of the script, with comments
7. The final DO_FLOW command, including debugging display options send("DO_FLOW, 49, 50")
8. Script overhead commands to complete the execute function, including final “}” action.setExitCode(0); action.setResultText("done."); out("Parameter parameter set up complete"); return action; }
9. Definition of script routine that actually sends MQTT messages to Hexbot via broker, and echoes it to MQTT.fx download window function send(cmd){ out(cmd); mqttManager.publish(myTWIPe, cmd); Thread.sleep(200); // occasionally lose a line if it's reduced to 100 }
10. Routine to send comments to MQTT.fx client display while script is downloading function out(message){ output.print(message); }

The easy way to include the script overhead is to start with a working script, replace the FLOW related commands, and update other fields as needed.

### Prepare for Testing

- consider whether or not you want 5 volt power connected to PWM board for initial tests

- verify that the last toeMoveAction parameter in the final DO_FLOW command has the right outputs enabled. The 16 and 32 bits are useful for debugging and graphing toe movements

- if you’re operating tethered, make sure there’s enough slack in your cables to accommodate the movement of the Hexbox as it executes the script.

- check that the surface the Hexbot will move on is suitable. Glossy, slippery surfaces often result in toe slippage which compromises movement.

- you might want to have a copy of the flow-tracker.ods file handy so that pasted console output can be used for debugging

### Do Test Run

- it’s recommended that you do your initial testing without enabling toe movement (either in the final DO_FLOW command, or by disabling 5 volt power). This will allow you to check for toe safety violations, and to view the Calc graph of the toe movements without any risks to servos.

- decide how much of your flow you want to test at a time. Doing smaller sections makes it easier to observe, and the toe graphs are easier to interpret.

- Use the /* ... */ commenting directives in the script file to remove other flow commands that you don’t want to execute yet.

- be prepared to quickly disable the 5 volt power to the PWM boards if something goes wrong and one or more servos are trying to achieve an impossible position. This may save a servo that otherwise might burn out.

- watch the current and voltage levels going to the PWM boards. If they get out of range, kill the 5 volt power and investigate.

- if you run into problems, adjust the position of the /* .. */ to narrow down how much of your script is executing and which flow row(s) are problematic.

-another way to narrow down where a problem is occurring is to capture the necessary data to do a Calc plot, and hide data rows to gradually expose were the toes are going on the graph.

### Check for Toe Safety Box Violations

If the execution of your flow stops suddenly with no apparent reason, it may be due to a toe safety violation. Every time a toe position is calculated, a sanity check is done to make sure it’s a safe position that’s unlikely to collide with the chassis, or another leg.

In order to be considered safe, a position must be within a box which has the leg’s home position approximately at its center. Six parameters control the size of this box, or how far the toe can be away from the home position and still be considered safe.

safeMaxPosX = 6; // max allowed displacement from home on positive local X axis

safeMaxNegX = 8; // max allowed displacement from home on negative local X axis

safeMaxPosY = 11; // max allowed displacement from home on positive local Y axis

safeMaxNegY = 6; // max allowed displacement from home on negative local Y axis

safeMaxPosZ = 6; // max allowed displacement from home on positive local Z axis

safeMaxNegZ = 8; // max allowed displacement from home on negative local Z axis

If a toe safety violation is detected, the console will have messages like this:

****************** toe safety violation(s) [<leg><coord><positive or negative side> : 1XN 3YP

followed by a display of all the toe positions.

The string at the end of the error message indicates where the violation occurred:

As indicated in the error message, 1XN 3YP means

Leg 1, X coordinate, exceeded the limit in the Negative direction

Leg 3, Y coordinate, exceeded the limit in the Positive direction

### Graph the Toe Movement

Being able to see where the toes are being positioned in a 2D overhead view can be very helpful in visualizing what the robot is actually doing, and where the actual behaviour diverges from the planned behaviour.

This can be done in a process with 2 phases:

1. run the script with a parameter set so that the global X and Y coordinates of each toe’s calculated position, for every frame, is displayed on the console (in MQTT in future?)
2. paste this data into a pre-built LibreOffice Calc spreadsheet which generates the graphical representation, and provides ways to zero in on toe movements of interest.

The steps to achieve this are:

- set up the toe-action parameter in the final DO_FLOW command in your script. 16 bit enables graphable output, and 32 is handy too, to get a nicely formatted flow display.
- to be safe, you may want to disable toe movement, via the 1 bit in toe-action, or by disabling 5 volt power. Neither impacts the generation of debug displays
- review other considerations in the Prepare for Testing & Do Test Run sections above
- run the script and generate the graphable data.
- copy the graphable output near the end of console output that starts with 00/
- paste it into cell A56 of a copy the graph sheet in ../docs/MQTT scripts/flow-tracker.ods
- the toe positions will appear in the graph at the top of that sheet

NOTES:

- The Calc chart is a top view of the Hexbot, and the forward direction is to your right. Leg 1 is in the bottom right

- the height of the toe, it’s global Z coordinate, is ignored. You’ll see toe positions marked on the graph if the toe is on the floor, or it it’s in the air.

-the home positions for each leg appear as pink filled in circles

- the numbers on the left of the data below the chart are the flow row numbers. Same numbers (starting at 0 ) as the nicely formatted flow display. Flow row numbers often appear multiple times, because there’s a display for every frame within the flow row.

-to zero in so the graph only shows a small number of toe movements, use the CALC “hide rows) feature to remove the rows before and after the specific ones you’re interested in. You can also “un-hide” the rows one at a time to see location for each frame.

### Run the Script with Movement Enabled

You’ve completed your testing, and are ready to let the robot actually move. Here’s a checklist of things to think about:

- make sure you’ve enabled toe movements in the last argument of the final DO_FLOW command in your script. While you’re at it, you might as well enable debug displays with the 16 and 32 bit values, for a total of 49.
- if you removed 5 Volt power to the PWM boards during testing, time to re-enable it
- be prepared to disable the 5 volt power quickly if servos start doing strange things, to reduce the chance that they’ll burn out
- if your robot lives on a test stand so it’s legs don’t touch the floor, that’s not a bad idea for initial testing. Otherwise, position the bot in the center of your test area.
- Hopefully, that test area has a no-slip surface
- if you’re operating from a battery, make sure it’s charged up
- If you’re operating tethered make sure the cables are positioned to allow the Hexbot’s expected movement without getting too tight.
- If you’re really optimistic, set up to capture video of the Hexbot’s performance. (Watching it in slow motion might help with troubleshooting?)

### Troubleshoot Unexpected Behaviours

Sections 8 through 11 in this document describe techniques you can use to troubleshoot any problems that arise. Some of the main ones are:

- Use the formatted flow display (toeMoveAction option 32) for a more readable view of your script. You can paste it into the second sheet of flow-tracker.ods to preserve it.
- Test your script in small pieces, using the /* .. */ commenting directives in the script to limit what you’re working on.
- If the script seems to have stopped with no explanation, check the console for toe safety violations.
- Graph the toe movements using the instructions in section 11, and zero in on the FLOW commands and frames with unexpected behaviour
- Monitor measurements of the servo current and voltage for anomalies.
- Tip: If the Hexbot crashes and reboots when you run your script, check for missing commas in the script.

### Document the Script

When a script is completed, or while it’s in development, these files should appear in Git:

- A folder with the script’s name under .../docs/MQTT Scripts

Within that folder you should have:

- a well commented copy of the script, as a .js file
- video files of the Hexbot executing the script (top view and side view)
- a copy of flow-tracker with both sheets completed
- documentation files describing the math used to build the script
- any spreadsheets that were used to generate numbers for the script

### Reference Information

#### Global Coordinates of Key Locations

#### Local Coordinates for Home Position (same for all legs)

X = 13.78, Y = -10.60, Z = 0

#### Operations Field in FLOW Commands

fo_moveAbs = 1; // move to absolute location, coords are in global system

fo_moveLocal = 2; // move to location given in local coords

fo_moveGRelHome = 3; // move to loc'n relative to home, #’s= GLOBAL deltas relative to home

fo_moveLRelHome = 4; // move to loc'n relative to home, #’s= LOCAL deltas relative to home

fo_moveRelLast = 5; // move to loc'n relative to last pos’n, #’s= deltas w.r.t. last pos’n

fo_startAbs = 6; // start of flow - go directly to an absolute location

fo_startRelHome=7; // start of flow - go directly to a position relative to home position

fo_startPrev = 8; // start flow, treating end of last flow as previous position

fo_markCycleStart=9; // this flow row # is beginning of a numbered cycle within the flow

fo_markCycleEnd =10; // this flow row number is the end of a numbered cycle within the flow

fo_doCycle = 11; // execute the specified cycle for the specified number of iterations.

#### Toe-Action Coding in Final DO_FLOW Command

fa_moveServos = 1; // feed calculated PWM values to servo motors so they move

fa_dispAngles = 2; // display the calculated servo angles (degrees) in serial monitor

fa_dispPWM = 4; // display the calculated PWM values

fa_dispLocal = 8; // display the local coordinates of toe position

fa_graphPrint = 16; // output each toe position suitable for Calc scatter plot graph

fa_dispFlow = 32; // display script’s flow commands in readable format before execution

### Example FLOW Commands

Here’s a reference diagram for the following examples. It’s a top view of the Hexbot, with the front of the robot facing the right. The positions of the hip servos, and the home positions are indicated, and the grid has 1 centimeter spacing. Our examples will involve Leg 1, which is in the bottom right corner of this diagram.

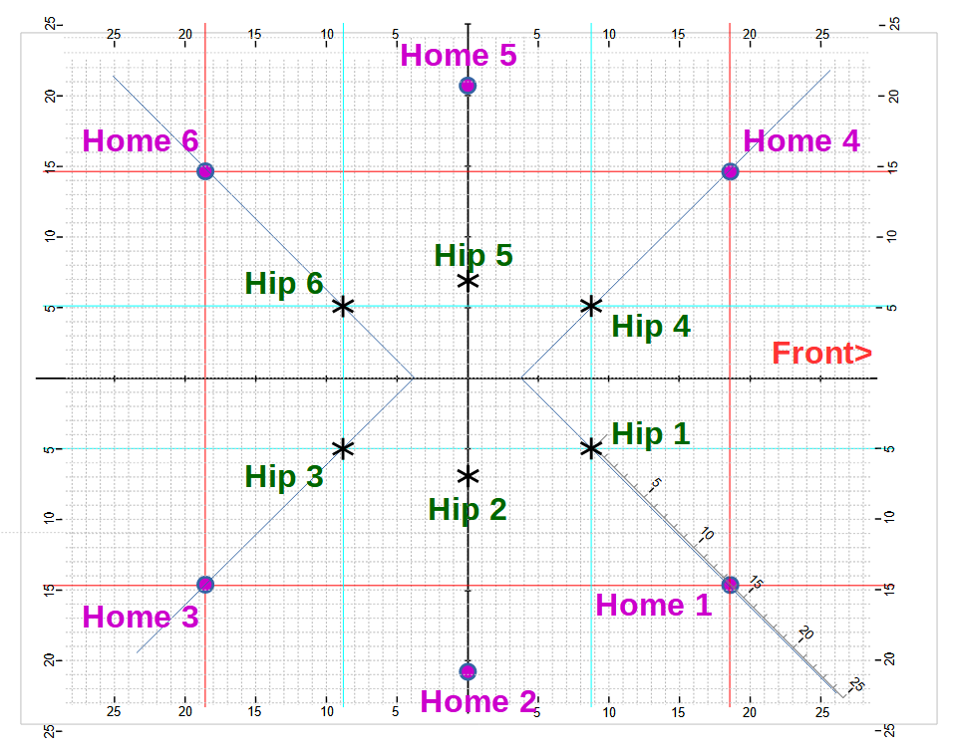
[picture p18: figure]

#### Move leg 1 to its home position

Using operation code 1, where the numbers are global coordinates:
FL,1000,1,10,0,0,0, 18.62, -14.79, -10.60, ...

Explanation: Direct use of the global coordinate system. (The easy way is to look this up in section 15.1.) The scales on the edges of the above diagram show global X and Y coordinates.

Using operation code 2, where the numbers are local coordinates:
FL,1000,1,10,0,0,0, 13.78, -10.60, 0, ...

Explanation: The local origin is above the leg’s hip servo, at the same height as the center of the knee servo. The X value is the sum of the lengths of the thigh ( 2.92) plus the shin (7.72) plus the toe offset(3.23) = 13.78. The Y value is the length of the foot, and it’s negative because it’s below the origin, -10.60. Since the home position occurs when the hip servo is at its center, the Z coordinate is 0. (Or, you could look it up in section 15.2 .) Here’s an illustration showing the local coordinate axes in blue:

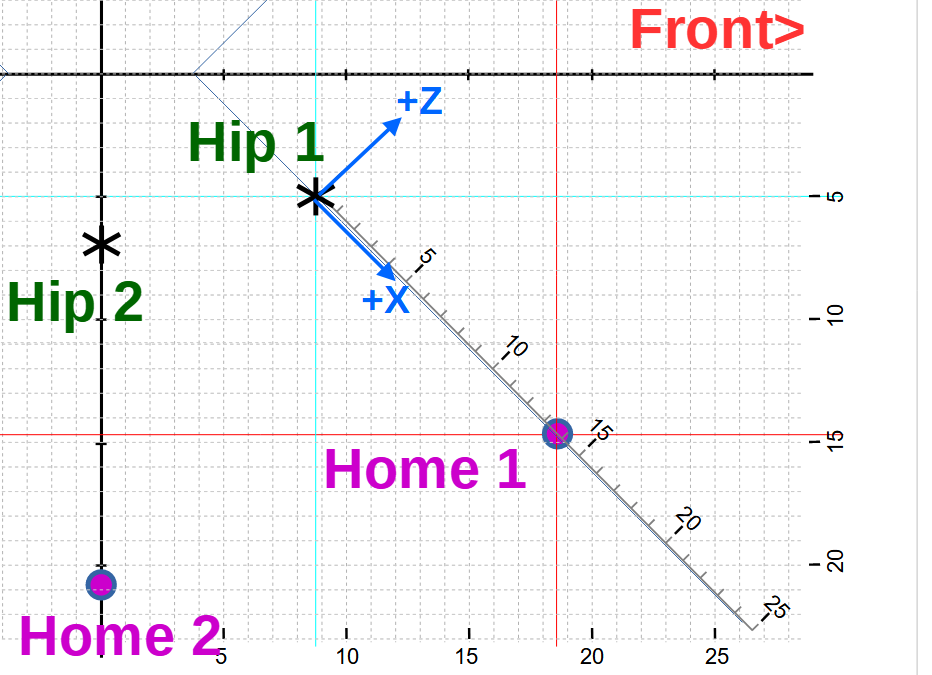
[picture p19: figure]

Using operation code 3, where numbers are global coordinate deltas relative to home pos’n
FL,1000,1,10,0,0,0, 0, 0, 0, ...

Explanation: This operation code uses numbers relative to the home position, i.e. the numbers are offsets from home in the global coordinate directions. Since we want the home position itself, the offsets are zero.

Using operation code 4, where numbers are local coordinate deltas relative to home pos’n
FL,1000,1,10,0,0,0, 0, 0, 0, ...

Explanation: This operation code also uses numbers relative to the home position, i.e. the numbers are offsets from home in the local coordinate directions. Since we want the home position itself, the offsets are zero.

#### Move leg 1 to a position 4 Cm in front of its home position

NOTE: “in front of” means towards the front of the robot, in the global +X direction. In this diagram of Leg 1’s corner, this target position is indicated by a red filled in circle.

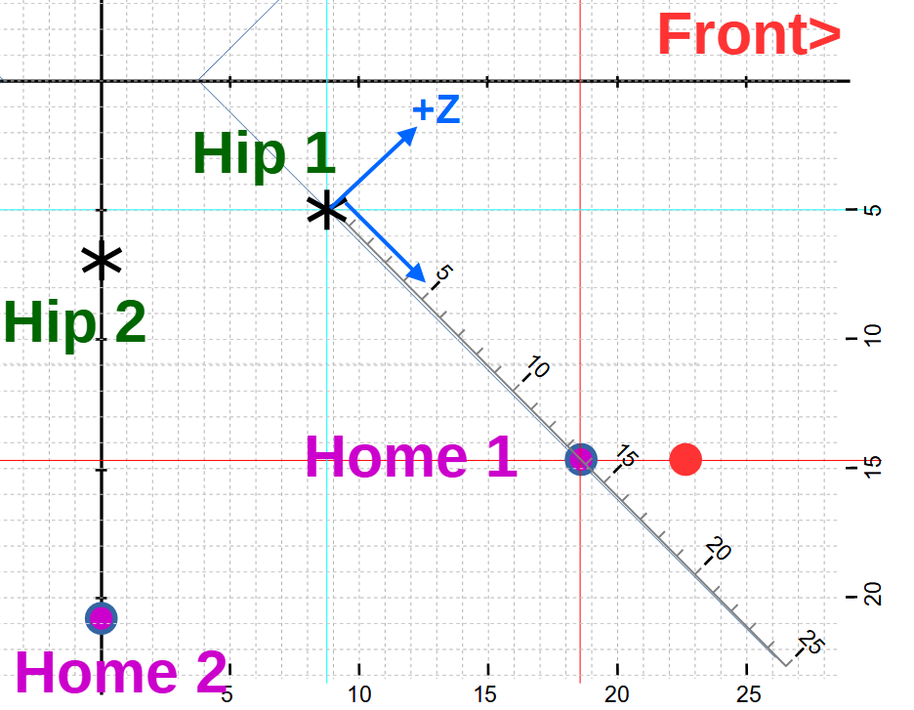
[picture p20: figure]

Using operation code 1, where the numbers are global coordinates:
FL,1000,1,10,0,0,0, 22.62, -14.79, -10.60, ...

Explanation: Direct use of the global coordinate system plus an offset in the global X direction. We take the known global coordinates for the home position, and add 4 to the X coordinate.

Using operation code 2, where the numbers are local coordinates:
FL,1000,1,10,0,0,0, 16.61, -10.60, 2.83, ...

Explanation: The offset isn’t aligned with the local coordinates, so we’ll end up changing both the local X and Z coordinates of the home position. Here’s an illustration of how we break the offset down to a combination of local X and Z changes:

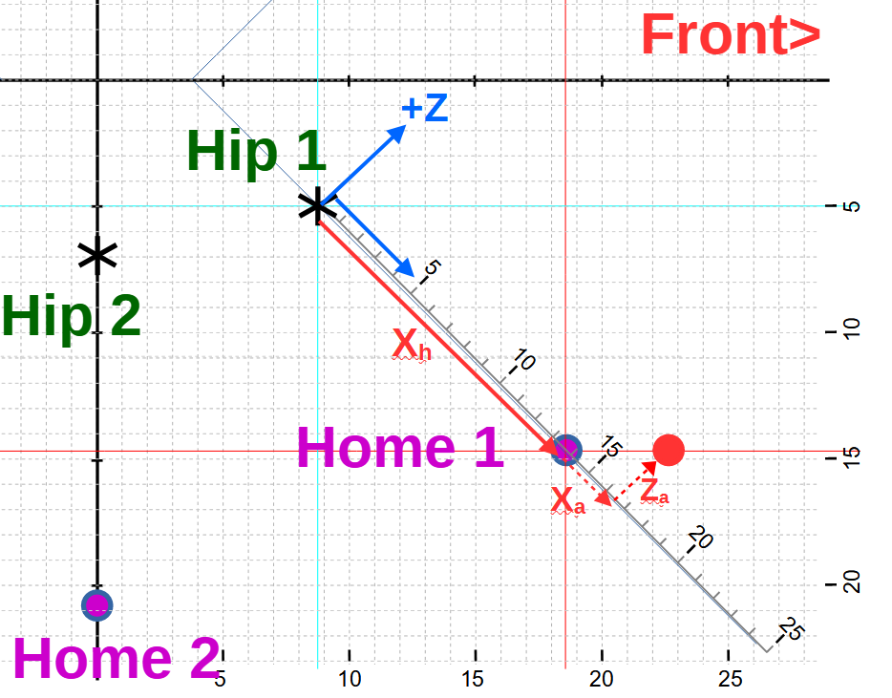
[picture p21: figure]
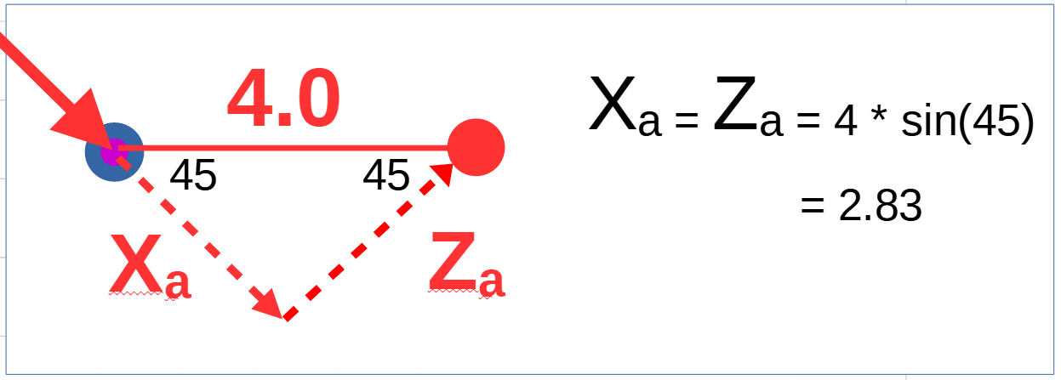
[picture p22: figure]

Zeroing in on the adjustments we need to make from the home position to get to the target...

Xa is what we need to add to the home position’s X coordinate, and Za is what we need to add to it’s Z component. Thus, the new coordinates are:

X = 13.78 + 2.83 = 16.61
Z = 0 + 2.83 = 2.83

Using operation code 3, where numbers are global coordinate deltas relative to home pos’n
FL,1000,1,10,0,0,0, 4, 0, 0, ...

Explanation: This one is easy, because it’s based on the home position, and it uses global coordinate offsets, same as the way our target location is defined. We have a 4.0 cm offset in the global +X direction, and no other offsets.

Using operation code 4, where numbers are local coordinate deltas relative to home pos’n
FL,1000,1,10,0,0,0, 2.83, 0, 2.83, ...

Explanation: As with operation code 2, we need to adjustments to the local coordinates needed to achieve the target offset of 4 cm in the global X direction. All the same calculations apply, but in the flow command, we just include the adjustments relative to the home position, rather than recalculated local coordinates.

### Example Flow Script -Taking A Step

A frequent Hexbot operation is taking a step that moves the robot a small amount relative to the floor. We’re going to build on our previous examples to create a script that moves the Hexbot forward by 4 cm. However, because we work in the perspective of the robot, it’s much easier to think that we’re pushing the floor backwards.

The entries that need to be included in every script are described in section 7 Putting Flow Commands into a Script . We’ll assume you will follow that, and we’ll concentrate on the flow commands that achieve the step.

While taking a step, one group of legs must be on the floor, perhaps moving, while the other set of legs is above the floor, repositioning for its turn on the floor. These groups need to be able to support the robot on their own. Using the sets (1,2,3) and (4,5,6) wouldn’t work, because all the legs on one side would be raised at the same time and the robot would be unstable. A better grouping is to use the odd numbered legs for one group, and the evens for the other: (1,3,5) and (2,4,6) . Each of these groups forms a large triangle on the floor, which can support the robot in a stable way. From now on, I’ll refer to these groups as the odds and the evens.

#### The Sequence of Actions

A logical sequence of actions for this movement might be:

1. start with all legs in the home position
2. lift the odds off the floor
3. move them 4 cm towards the front of the Hexbot
4. lower the odds
5. lift the evens
6. pull the odds back to the home position, moving the robot 4 cm forward
7. ...repeat to move another 4 cm ...

We’ve now met the goal of moving forward 4 cm, but not very efficiently. The robot is only moving relative to the floor in one of the 6 stages, and we haven’t used the evens at all.

This sequence takes 10 stages to move 8 cm.

We can make use of the fact that all six legs can move in every flow command to improve this sequence of stages:

1. start with all legs in the home position
2. lift the odd legs off the floor
3. move the evens 4 cm backwards
4. lower the odds
5. raise the evens
6. move the odds 4 cm backwards, and return evens to be over home positions
7. lower the evens
8. raise the odds
9. move the evens 4 cm backwards, and return the odds to be over the home position
10. .. repeat ...

This improved sequence takes 6 stages to move 8 cm, and movement is almost continuous. There are still improvements we could make to this sequence, but let’s get the basic flow script working first.

To decide which type of flow operation we want to use, we look at the nature of the motion. In this sequence, all of the motion (other than up and down) is movement of legs in the plus and minus global X direction. It’s also all focused on the home positions. So it seems like using operation 3, when the numbers for each leg are offsets from the home position using global coordinates would be efficient. Next we need to create flow commands for each stage in our improved sequence. We’ll start with one second durations for each flow, which makes it easier to observe and interpret the robot’s actions. We can optimize the timing later.

#### Converting Actions to Flow Commands

Stage 1: start with all legs in the home position

We can use either of the operation codes that are based on the home position, and give zero offsets, so we’re left with just the home position:

FL,1000,3,10,0,0,0, 0,0,0, 0,0,0, 0,0,0, 0,0,0, 0,0,0, 0,0,0

Stage 2: lift the odd legs off the floor

The 3rd global coordinate is Z which is up and down. Up is positive, so we can raise the legs (just the odds) by using an offset of 2 in the third coordinate of those legs.

FL, 1000, 3, 10,0,0,0, 0,0,2, 0,0,0, 0,0,2, 0,0,0, 0,0,2, 0,0,0

Stage 3: move the evens 4 cm backwards

This is where using operation code 3 pays off. We just put the offset of -4 cm into the X coordinate for the evens. We also have to keep the odds in the air, so we maintain what we did in the previous flow. This stage moves the robot forward.

FL, 1000, 3, 10,0,0,0, 0,0,2, -4,0,0, 0,0,2, -4,0,0, 0,0,2, -4,0,0

Stage 4: lower the odds

The 3rd global coordinate is Z which is up and down. We’re undoing what we did in stage 2, but maintaining the positions of the other legs

FL, 1000, 3, 10,0,0,0, 0,0,0, -4,0,0, 0,0,0, -4,0,0, 0,0,0, -4,0,0

Stage 5: raise the evens

Same old use of the 3rd coordinate, but for the even legs, conserving everything else

FL, 1000, 3, 10,0,0,0, 0,0,0, -4,0,2, 0,0,0, -4,0,2, 0,0,0, -4,0,2

Stage 6: move the odds 4 cm backwards, and return evens to be over home positions

The odds are going backwards, so their X offset is -4. The evens are coming back to the home position, still in the air, so their X offset is 0. This stage moves the robot forward.

FL, 1000, 3, 10,0,0,0, -4,0,0, 0,0,2, -4,0,0, 0,0,2, -4,0,0, 0,0,2

Stage 7: lower the evens

So we get rid of their +2 offset and put them back to the home position

FL, 1000, 3, 10,0,0,0, -4,0,0, 0,0,0, -4,0,0, 0,0,0, -4,0,0, 0,0,0

Stage 8: raise the odds

OK, so their Z offset, third coordinate will be 2

FL, 1000, 3, 10,0,0,0, -4,0,2, 0,0,0, -4,0,2, 0,0,0, -4,0,2, 0,0,0

Stage 9: move the evens 4 cm backwards, and return the odds to be over the home position

Like step 6, but the roles of the evens and odds are reversed. This stage moves the robot forward.

FL, 1000, 3, 10,0,0,0 0,0,2, -4,0,0, 0,0,2, -4,0,0, 0,0,2, -4,0,0

#### Consolidated Flow Listing

Here’s what we ended up with. See ../docs/MQTT scripts/onestep for an executable version.

1. FL, 1000, 3, 10,0,0,0, 0,0,0, 0,0,0, 0,0,0, 0,0,0, 0,0,0, 0,0,0
2. FL, 1000, 3, 10,0,0,0, 0,0,2, 0,0,0, 0,0,2, 0,0,0, 0,0,2, 0,0,0
3. FL, 1000, 3, 10,0,0,0, 0,0,2, -4,0,0, 0,0,2, -4,0,0, 0,0,2, -4,0,0
4. FL, 1000, 3, 10,0,0,0, 0,0,0, -4,0,0, 0,0,0, -4,0,0, 0,0,0, -4,0,0
5. FL, 1000, 3, 10,0,0,0, 0,0,0, -4,0,2, 0,0,0, -4,0,2, 0,0,0, -4,0,2
6. FL, 1000, 3, 10,0,0,0, -4,0,0, 0,0,2, -4,0,0, 0,0,2, -4,0,0, 0,0,2
7. FL, 1000, 3, 10,0,0,0, -4,0,0, 0,0,0, -4,0,0, 0,0,0, -4,0,0, 0,0,0
8. FL, 1000, 3, 10,0,0,0, -4,0,2, 0,0,0, -4,0,2, 0,0,0, -4,0,2, 0,0,0
9. FL, 1000, 3, 10,0,0,0, 0,0,2, -4,0,0, 0,0,2, -4,0,0, 0,0,2, -4,0,0

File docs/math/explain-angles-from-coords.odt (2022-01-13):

Deriving servo angles from local coordinates of toe ver 6

Task: Given the location of the toe at point T = (Tx, Ty, Tz), find the servo rotation angles for the hip Rh, knee Rk and ankle Ra with angles expressed in degrees.

General approach: Find the coordinates of the ankle (Ax, Ay, Az) and from there, calculate the angles.

Finding the hip angle is straight forward. Looking down from above, the leg’s projection in the local xz plane is a straight line that is the hypotenuse of a right angled triangle with the X axis, with the hip angle between these 2 lines. Therefore:

tan(Rh) = Tz/Tx, or Rh = arctan(Tz/Tx) // in spreadsheet & program, ATAN2(y,x) function, as ATAN2(Tz, Tx), different arg order

Based on this, we can use Rh in calculating the ankle coordinates.

To reduce the 3D problem to 2D, envision rotating the hip servo so its angle is zero, and the leg is sticking straight sideways.

Viewing from the top again, we have a plane that’s like (x,y) coordinates but in our case, the traditional x axis is the local z axis, and the traditional y axis is the local x axis, negated.

The formula for rotating a 2D vector (x,y) through a counter clockwise angle beta is:

(x,y) --> ( x*cos(beta) - y*sin(beta) , x*sin(beta) + y*cos(beta) )

to apply this to the path of the toe in our case, we have to:

- account for our angle being clockwise.

Although the rotation of the hip servo Rh is positive when going counter clockwise, the rotation we’re doing to the toe is opposite to that, clockwise. We negate it to change direction and get -Rh counter clockwise.

Our rotation formula requires that the angle be expressed as counter clockwise, so for beta in the formula, we’ll use -Rh.

- account for our different coordinates

Using the pivot point as the origin (which fortunately is the origin of the local coordinate system as well), to rotate the toe vector, we get:

traditional x value for toe vector is Tz, the toe position’s local z coordinate

traditional y value for toe vector is -Tx, the toe position’s local x coordinate negated.

if (Ux, Uy, Uz) represents the rotated position of the toe, then:

Ux = the rotated toe point’s y coordinate, negated (local positive x axis is in direction of traditional negative y axis)

= -1 * (x * sin(beta) + y * cos(beta) ) using traditional coordinates in rotation formula

= -1 * (Tz * sin(-1*Rh) + (-Tx) * cos(-1*Rh) ) using the equivalent in local coordinates

= Tx * cos(-1*Rh) – Tz * sin(-1*h) [0]

Uy = Ty // our rotation doesn’t change the y coordinate of any points

Uz = 0 // we selected our rotation to give this

Now let’s look at the plane where z = 0, containing our rotated leg sticking out sideways.

The ankle lies on a circle of radius 7.5 cm (body shin measurement, or BS) , centred on the knee which is 2.5 cm (body thigh measurement, or BT) from the origin,

above the hip servo, at y=0.

It also lies on a circle with radius 11 cm (body measurement diagonally across foot from ankle to toe, or BF), centred on the toe, at (Ux, Uy, Uz)

The formula for a circle is ( x - Xc)^2 + (y - Yc)^2 = r^2 where (Xc,Yc) is the center, and r is the radius

The equation for the first circle is:

(x - BT)^2 + (y - 0)^2 = BS^2

x^2 -2*BT*x + BT^2 + y^2 = BS^2 [1]

for the second circle:

(x - Ux)^2 + (y - Uy)^2 = BF^2

x^2 -2*x*Ux + Ux^2 + y^2 -2*y*Uy + Uy^2 = BF^2 [2]

(y - Uy)^2 = BF^2 - (x - Ux)^2, y = +/- sqrt( BF^2 - (x - Ux)^2 ) + Uy [3]

subtracting equation [2] from equation [1]...

x^2 - 2*BT*x + BT^2 +y^2 -x^2 + 2*x*Ux -Ux^2 -y^2 +2*y*Uy -Uy^2 = BS^2 - BF^2

x^2(1-1) +x(-2BT+2*Ux) +y^2(1-1) +y(2*Uy) + BT^2 -Ux^2-Uy^2 = BS^s - BF^2

x(-2BT+2*Ux) +y(2*Uy) + BT^2 - Ux^2 - Uy^2 = BS^s – BF^2

y = (BS^2 – BF^2 + Ux^2 + Uy^2 – BT^2 +x*(2BT -2Ux) ) / (2 * Uy) [3]

substituting y as defined by [3] back into equation [1]

x^2 - 2 * BT*x + BT^2 + y^2 = BS^2 [1]

x^2 - 2 * BT*x + BT^2 + ( (BS^2 – BF^2 + Ux^2 +Uy^2 – BT^2 + x*(2*BT – 2*Ux) ) / (2 * Uy) )^2– BS^2 = 0

since BS, BF, Ux, Uy and BT are fixed constants for given toe position, we can treat algebraic combinations of them as a single coefficient

thus we define C1 = BS^2 – BF^2 + Ux^2 + Uy^2 - BT^2

and C2 = 2*BT – 2*Ux

x^2 – 2*BT*x + BT^2 + ( C1 + x* C2 )^2 - BS^2 = 0

(2*Uy)^2

x^2 – 2*BT*x + BT^2 + ( C1^2 + 2*C1*x*(C2) + x^2*C2^2) - BS^2 = 0

(2*Uy)^2

x^2*(1 + C2^2 ) + x*( -2*BT + 2*C1*C2 ) + ( BT^2 + C1^2 - BS^2 ) = 0 [4]

4*Uy^2 4*Uy^2 4*Uy^2

which is a quadratic equation in x, of the form ax^2 +bx + c = 0, with solutions ( - b +/- SQRT( b^2 - 4*a*c) / (2*a) //note the +/-, which gives 2 solutions (sometimes)

a = 1 + C2^2/(4*Uy^2)

b = -2*BT + (2*C1*C2)/(4*Uy^2)

c = BT^2 + C1^2/(4*Uy^2) – BS^2

where

C1 = BS^2 – BF^2 + Ux^2 + Uy^2 -BT^2

C2 = 2*BT – 2*Ux

BS = body’s shin length

BF = body’s foot length (diagonal from ankle to toe)

BT = body’s thigh length

Ux = toe’s local X coordinate when projected onto local XY plane

Uy = toe’s local Y coordinate when projected onto local XY plane

Rh = hip rotation angle, positive is counterclockwise seen from above

BTOA = Body’s Toe Offset angle, approximately 17 degrees

BTOD = Body’s Toe Offset Distance, approximately 3.2 cm

In the general case, equation [4] gives 2 possible values for x due to the +/- choice. Equation [1] implies there are 2 possible y values for each, but equation [3] implies there is just one. Having 2 overall solutions seems appropriate, since the circles centred at the toe and the knee intersect in at most 2 points.

( Bring on the spreadsheets. Warning: spreadsheet ATAN2 function has different arg order than C++ )

So, when the dust settles we have possible values for (x,y), the local coordinates for the ankle. One corresponds to the choice of “plus” in the quadratic solution, designated by a “P” in spreadsheet variable names, and “M” represents the choice of minus. In each case, equation (3) is used to derive a single value for y.

The knee angle Rk is straightforward to calculate once we know that the ankle is (x, y):

Rk = arctan( (y)/ (x - BT) ) // note that the knee is horizontally displaced from the origin by the thigh, thus the (x – BT) in the formula

The angle at the ankle is complicated because the toe is not in line with the servo’s zero position, but is about 17 degrees (Body Toe Offset Angle = BTOA) from it, away from the robot’s chassis. It also gets moved by the knee rotation.

If we temporarily ignore the offset , we can calculate the ankle angle R’a using either it’s arcsin or arctan function:

R’a = arcsin( (Ux – x) / BF ) , or

R’a = arctan( Ux – x) / ( y – Uy) )

This angle is composed of the BTOA 17 degree offset, the contribution due to knee rotation which is -ve, and the ankle rotation..

Thus Ra = R’a – 17 degrees - (-Rk)

= arctan( Ux – x) / ( y – Uy) ) - BTOA + Rk

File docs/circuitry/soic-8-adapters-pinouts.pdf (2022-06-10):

SOIC-8 to DIP-8 Adapters

## VN7050ASTR

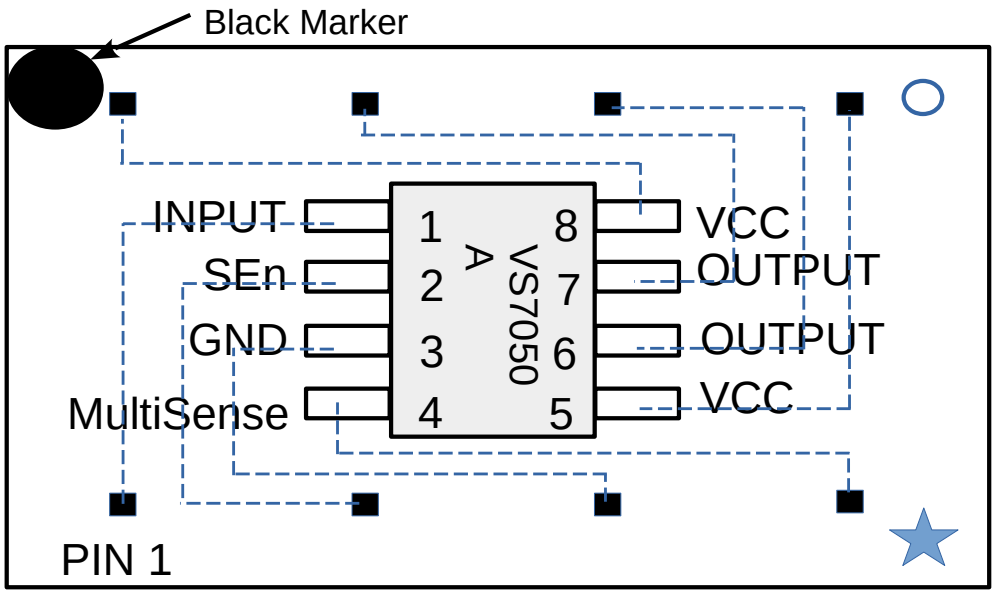
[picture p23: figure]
VCC OUTPUT OUTPUT VCC; SEn; INPUT; GND MultiSense; Black Marker; PIN 1

## STMPS2141MTR

Pin 8: VCC
battery connection

Pins 6 & 7: OUTPUT
Power outputs

Pin 3: GND
Ground

Pin 1: INPUT (GPIO)
Switch control 3.3 or 5V

Pin 4: MultiSense
Analog current sense

Pin 2: SEn
Multisense enable

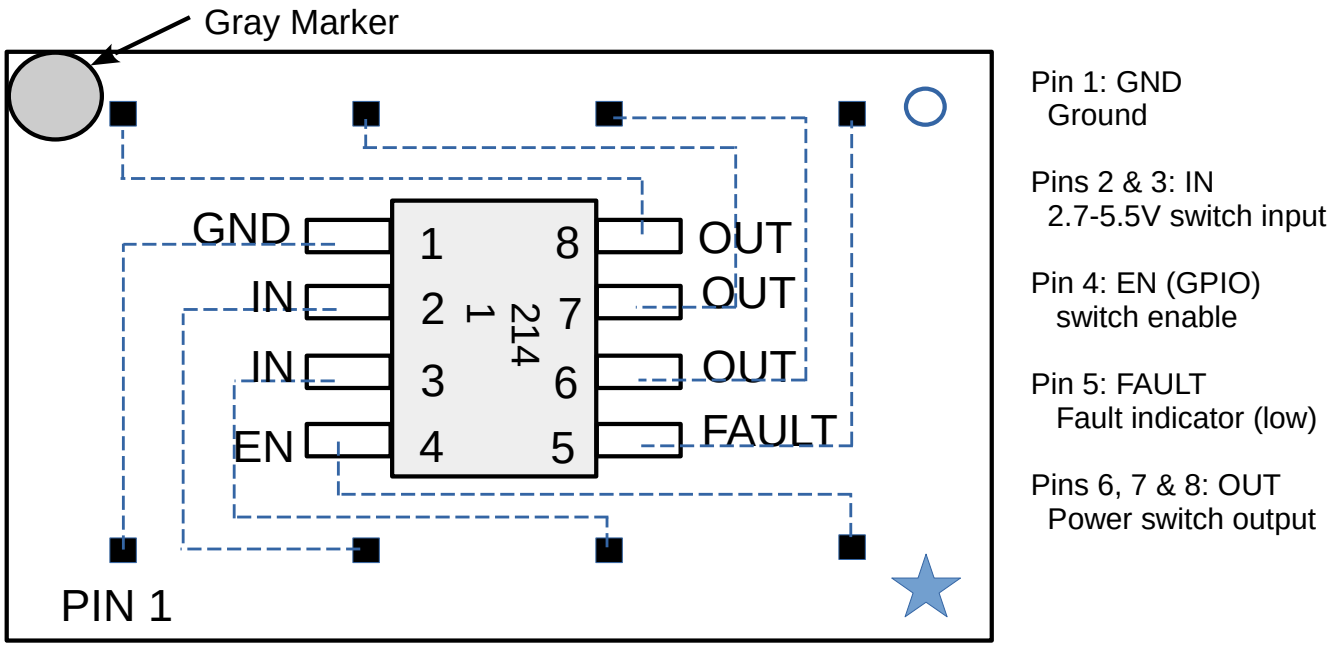
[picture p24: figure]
PIN 1; OUT OUT FAULT; GND; Gray Marker; OUT; Pin 1: GND Ground; Pins 2 & 3: IN 2.7-5.5V switch input; Pin 4: EN (GPIO) switch enable; Pin 5: FAULT Fault indicator (low); Pins 6, 7 & 8: OUT Power switch output

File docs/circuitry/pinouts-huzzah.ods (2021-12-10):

PINOUTS FOR THE Adafruit ESP32 Feather Module in the HexBot
Adafruit ESP32 Phys. pin | Gpio | GPIO Name | Silkscreen to GPIO | Pin Functions (A/D, I2C, SPI, serial...) | Connection/Function in the HexBot
1 |  |  |  | RESET
2 |  |  |  | 3V | To both PCA9685 Vcc pins
3 |  |  |  | n/c
4 |  |  |  | CPU GND | to both PCA9685 GND pins
5 | 26 |  | PIN_LBL_A0 | A0/AD2, GP26,DAC2
6 | 25 |  | PIN_LBL_A1 | A1/AD2, GP25,DAC1
7 | 34 |  | PIN_LBL_A2 | A2/AD1, GPio34
8 | 39 |  | PIN_LBL_A3 | A3/AD1, GPio39
9 | 36 |  | PIN_LBL_A4 | A4/AD1, GPio36
10 | 4 |  | PIN_LBL_A5 | A5/AD2, GPio4
11 | 5 |  | PIN_LBL_SCK | SPI-SCK, GPio05
12 | 18 |  | PIN_LBL_MO | SPI-MO
13 | 19 |  | PIN_LBL_MI | SPI-MI
14 | 16 |  | PIN_LBL_RX | RX Serial1
15 | 17 | I2C_BUS1_SDA | PIN_LBL_TX | TX Serial1
16 | 21 | I2C_BUS1_SCL | PIN_LBL_21 | GPio21
17 | 23 | I2C_BUS0_SDA | PIN_LBL_SDA | I2C, GPio23 | I2C Bus0 to both PCA9685 PWM driver SDA pins. No pullup resistors?
18 | 22 | I2C_BUS0_SCL | PIN_LBL_SCL | I2C, GPio22 | I2C Bus0 to both PCA9685 PWM driver SCL (AKA SCE) pins. No pullup resistors?
19 | 14 | BUTTON_C | PIN_LBL_14 | A6/AD2, GPio14
20 | 32 | BUTTON_B | PIN_LBL_32 | A7/AD1, GPio32
21 | 15 | BUTTON_A | PIN_LBL_15 | A8/AD2, GPio15
22 | 33 |  | PIN_LBL_33 | A9/AD1, GPio33
23 | 27 |  | PIN_LBL_27 | A10/AD2, GPio27
24 | 12 |  | PIN_LBL_12 | A11/AD2, GPio12
25 | 13 |  | PIN_LBL_13 | A12/AD2, GPio13
26 |  |  |  | USB
27 |  |  |  | Enable
28 |  |  |  | LiPo Battery
 | (A13,GPio35) resistor divider linked to VBAT
 |  |  |  |  | fully programmable weak pullup / pulldown ( 14, 16, 17, 18, 19, 21, 22, 23)
 |  |  |  |  | powers up with weak pullUP enabled ( 5, 15)
 |  |  |  |  | powers up with weak pullDOWN enabled ( 4)
 |  |  |  |  | input only pins ( 34, 36, 39)
 |  |  |  |  | can be touch capacitive sensor ( 10, 19, 20, 21, 22, 23, 24, 25)

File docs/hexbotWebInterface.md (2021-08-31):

# Hexbot Web Interface

Hexbot features a 2.4GHz 802.11n [WiFi radio](https://www.juniper.net/documentation/en_US/junos-space-apps/network-director3.1/topics/concept/wireless-radio-channel.html) that requires a WiFi access point capable of communicating at 150Mbps. Hexbot hosts a [web server](https://en.wikipedia.org/wiki/Web_server) that can be used to configure values stored in non volitile memory (NVRAM) as well as perform over-the-air (OTA) firmware updates via a web browser.

<code>
  One quirk of the web interface is that each screen opens up a seperate tab. For this reason you should get in thhe habit of closing the tabs once you are done with them or you will get overwhelmed by screens during a busy session.
</code>

## Login Screen

<table>
  <tr>
    <td align ="center"> 
       <figure>
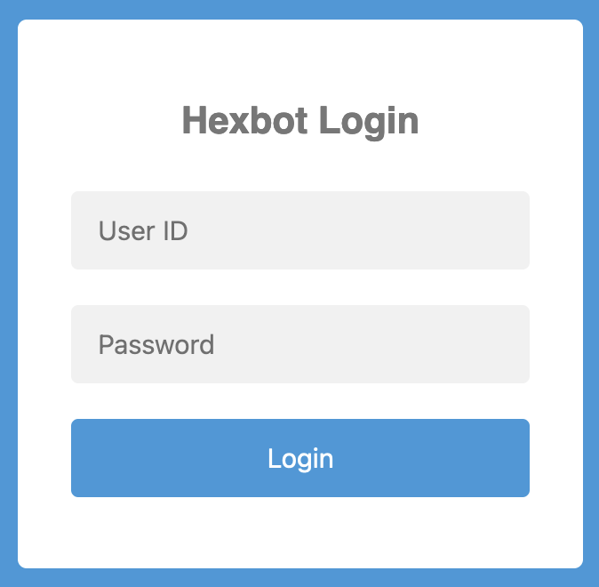
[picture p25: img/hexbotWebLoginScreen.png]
Login Screen
          <br>
          <figcaption>Fig.1 - Login Screen</figcaption>
       </figure> 
    </td>
    <td align ="left"> 
      In order to use Hexbot's web interface you must meet these conditions:
      <br><br>
      <ol>
        <li>Hexbot must be powered on and successfully connected to the local network.</li>
        <li>You will need the use of a web broswer on a computer that is also on the local network.</li>
        <li>You will need to know the IP address of Hexbot, which you can get using a couple of different methods.</li>
      </ol>
        Once you meet all of these conditions then open your web browser and enter Hexbot's IP address in the URL address field. You should be presented with the screen shown in figure 1. You are now talking directly to Hexbot via it's web interface. 
        <br><br>
        Security is a bit lax at present as the ID and password are hardcoded into the HTML sent to the client. With this in mind it is not too much of a security breach to tell you here that the login credentials are:
      <ul>
        <li>ID: admin</li>
        <li>Password: admin</li>
      </li>   
    </td>
  </tr>  
</table>

## Web Control Screen

<table>
  <tr>
    <td align ="center"> 
       <figure>
          Hexbot Config Updater Screen<br>
          <figcaption>Fig.2 - Web Control Screen</figcaption>
       </figure> 
    </td>
    <td align ="left"> 
      After successfully logging in you are prsented with the options menu shown in figure 2. There are minimal options available as this is a tool meant for initialization and maintenance tasks only. Your options are limited to:
      <br><br>
      <ol>
        <li>OTA - used to perform firmware updates.</li>
        <li>Config - used to tell Hexbot what the IP address of your network's MQTT broker is.</li>
      </ol>
    </td>
  </tr>  
</table>

## OTA Updater Screen

<table>
  <tr>
    <td align ="center"> 
       <figure>
          Hexbot Config Updater Screen<br>
          <figcaption>Fig.3 - Config Updater Screen</figcaption>
       </figure> 
    </td>
    <td align ="left"> 
      If you selected the OTA option on the Web Control screen then you will be presented with the Config Updater screen shown in figure 3. To perform OTA updates of Hexbot's firmware here is what you need to do.
      <br><br>
      <ol>
        <li>Find the firmware binary file that you want to upload. Normally you will find here: *<Hexbot project directory>/.pio/build/feather32/firmware.bin*. This example assumes that you are using the Huzzah32 development board. Note that when you pull source code from your [git remote origin](https://www.javatpoint.com/git-origin-master) this directory gets erased. To rebuild it simply run a build in PlatformIO.</li>
        <li>Click choose file. Navigate to the firmware.bin file.</li>
        <li>Click the Update button.</li>
        <li>You can watch the progress bar on the web page and/or watch the progress in a terminal window if you are hard wired into the Hexbot USB port.</li>
        <li>Check to see if the MQTT broker IP address is still OK. If not then reset it.</li>
      </ol>  
    </td>
  </tr>  
</table>

## Config Updater Screen

<table>
  <tr>
    <td align ="center"> 
       <figure>
          Hexbot Config Updater Screen<br>
          <figcaption>Fig.4 - Config Updater Screen</figcaption>
       </figure> 
    </td>
    <td align ="left"> 
      If you selected the Config option on the Web Control screen then you will be presented with the Config Updater screen shown in figure 4. The ony thing that you can configure via this interface it the IP address Hexbot will use to access an MQTT broker. Here is an outline of the workflow: 
<br><br>
<ol>
  <li>Enter a valid IP address and click the Update button.</li>
  <li>Hexbot does a rudamentary validation of the IP address by pinging it.</li>
  <li>If the address can be reached then you will see the message *Broker IP successfuly uppdated* on the web page and Hexbot updates it's flash memory with this value. If you have a terminal session connected to Hexbot's USB port then you will also see the messages in your console. See figure 5 for these messages. Note that flash memory persists through power off.</li>
  <li>If the address cannot be reached then you will see the message *Broker IP rejected. Keeping old address* on the web page and Hexbot discards your input. If you have a terminal session connected to Hexbot's USB port then you will also see the messages in your console. See figure 5 for these messages.</li>
</ol>
      
<figure>
  Console messages for broker IP change.<br>
  <figcaption>Fig.5 - Console messages for broker IP change</figcaption>
</figure> 
<br><br>      
<code>
  Normally you will only need to perform this task the first time that you change the network that Hexbot is connected to. It is a good idea to also check that the broker IP address is correct whenever you load new firmware onto your Hexbot.
</code>
    </td>
  </tr>  
</table>

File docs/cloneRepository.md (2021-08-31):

# Cloning the HexBot Repository

This page walks you through how to clone the HexBot GitHub repository to your local Git repository. 

If you are new to making VA3WAM projects and wish to emulate the local directory structure that we use then please read 
[this](https://va3wam.github.io/versionControl/#local-directory-setup).

## Step by step instructions

1. In a terminal window, navigate to the root of your local Git project directory. ```cd .../VisualStudioCode/PlatformIO/Projects```
2. Clone the remote origin server. ```git clone https://github.com/va3wam/hexBot.git```
3. Confirm that you now see a sub-directory off your local project directory named *hexBot*. 
4. Go into the hexBot directory (if you are not already there) and issue the command ```git remote```. If you get back the response *origin* then jump to step 6. If you get a blank response back then proceed to step 5.
5. Issue the command ```git remote add origin https://github.com/va3wam/hexBot.git``` to set up the remote. Now repeat step 4. 
6. At this point you have successfully cloned the Hexbot repository. Now you need to set up your PlatformIO IDE.

# Set up PlatformIO

1. In the hexBot directory create a file called platformio.ini.
2. Copy the content of the appropriate platform template from the [AA](/AA) directory. For MAC use [*platformIO-MAC-example.txt*](/AA/platformIO-MAC-example.txt).
3. Open Visual Studio Code. Make sure that there are no active projects or files open.
4. Navigate to the PlatformIO splash screen (use the house icon in the bottom left bar). Make sure that there are no active projects or files open.
5. Click the open project button.
6. Navigate to the hexBot directory.
7. Click the Open "hexBot" button. 
8. If you wish to work on this repository you will need to click the "Yes I trust the authors" button.
9. Assuming everything has gone well you are all set up with a local repository and an associated remote origin and you are ready to start developing your additions to the repository.

NOTE: Please do not work in the main branch but rather create branches in which to work. You can read about our prefered workflow [here](https://va3wam.github.io/versionControl/#git-workflow).

# Visual Studio Code Plugins

A quick note on Visual Studio Plugins. We recommand that you install the following:

1. [PlatformIO](https://marketplace.visualstudio.com/items?itemName=platformio.platformio-ide) (embedded system IDE).
2. [GitHub Pull Requests and Issues](https://marketplace.visualstudio.com/items?itemName=GitHub.vscode-pull-request-github) (Perform github tasks from VCS). See [this article](https://code.visualstudio.com/docs/editor/github).
3. [GitLens](https://marketplace.visualstudio.com/items?itemName=eamodio.gitlens) (shows full commit history inline in VSC).

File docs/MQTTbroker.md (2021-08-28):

# MQTT Broker

The Hexbot robot acts as an IoT Smart [Connected Product/Device](https://en.wikipedia.org/wiki/Smart_device).

## Communication
Hexbot features a 2.4GHz 802.11n WiFi radio that requires a WiFi access point capable of communicating at 150Mbps. You must also have a QOS1 capable MQTT broker listening on port 1883 on your network. Additionally, you must configure the MQTT Broker to support websocket connection on port 9001. Finally you must have a client device capable of running a web browser. This enables the robot to be remotely controlled via MQTT messaging over a WiFi link.

### MQTT Interface
Hexbot acts as an [MQTT](https://en.wikipedia.org/wiki/MQTT) client and supports a PUB/SUB interface that listens for messages on port 1883 encapsulated in IPv4 packets. The robot publishes and subscribes to/from topics via a broker usiing QOS1 MQTT messages encapsulated in TCP/IP packets. 

## MQTT Client
We use the MQTTfx client on out computer to issue [commands](mqttCommands.md) to Hexbot.

## Raspberry Pi Hosting Server
We host the MQTT on a Rapsberry Pi 3 Model B V1.2. 

```
cat /etc/os-release
PRETTY_NAME="Raspbian GNU/Linux 10 (buster)"
NAME="Raspbian GNU/Linux"
VERSION_ID="10"
VERSION="10 (buster)"
VERSION_CODENAME=buster
```

## Mosquitto Broker Software
We run the Mosquitto MQTT broker as a background daemon configured as follows.

```
mosquitto version 1.5.7 starting
1630104172: Using default config.
1630104172: Opening ipv4 listen socket on port 1883.
```

### Identification
The unqiue Media Access Control or [MAC](https://en.wikipedia.org/wiki/Medium_access_control) address of the radio prefixed by 'hexbot' is used to uniquely identify each hexbot robot to both the required WiFi Access Point and the MQTT broker. This makes it possible for multiple robots to co-exist in the same network.

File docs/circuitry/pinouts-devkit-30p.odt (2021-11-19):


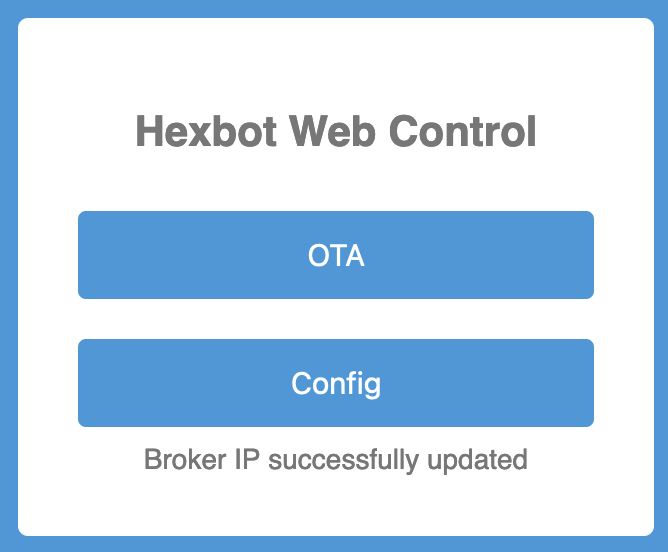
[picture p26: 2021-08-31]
img/hexbotWebScreenValidBrokerIP.png

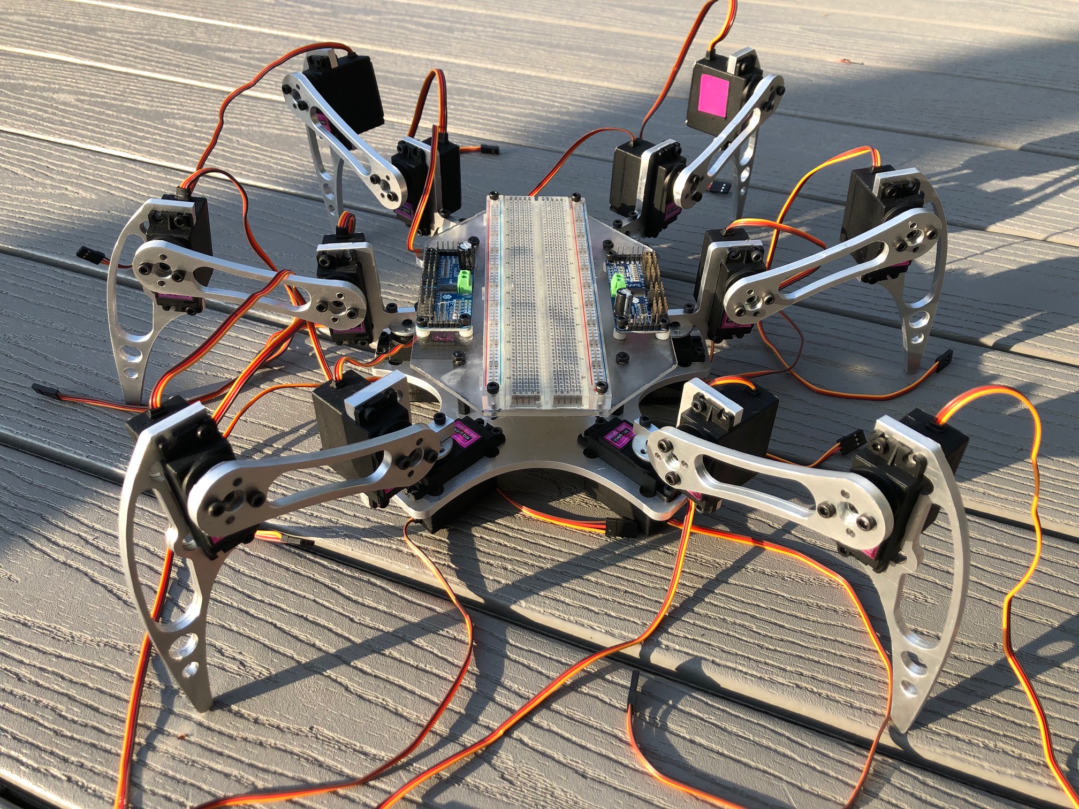
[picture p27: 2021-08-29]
img/topBodyLayer.jpg

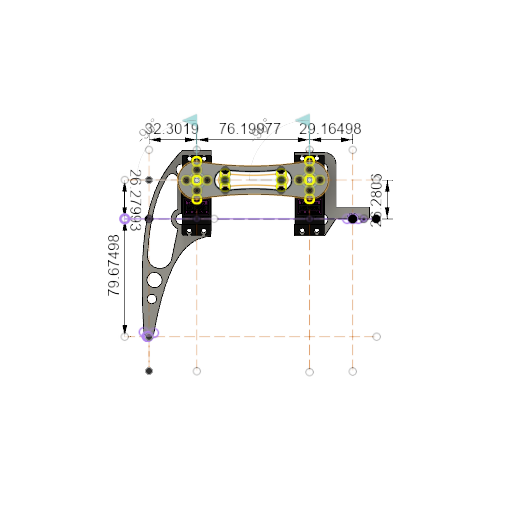
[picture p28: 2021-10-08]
img/frontViewModel.png

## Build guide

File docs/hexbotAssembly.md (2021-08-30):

# Hexbot Assembly Instructions

This document takes you through the steps neccessary to successfully assemble version 3 of the Hexbot robot.

## What you need

Before you start make sure that you have all [the hardware that you need](/docs/hexbotHardware.md).

## Step 1 - Assemble three right legs

Repeat the steps in this section three times in order to create the three right legs that we need. Make note of the orientation of the motors relative to the components that make up the leg in figure 1.

 <table>
  <tr>
    <td align ="left"> 
        <figure>
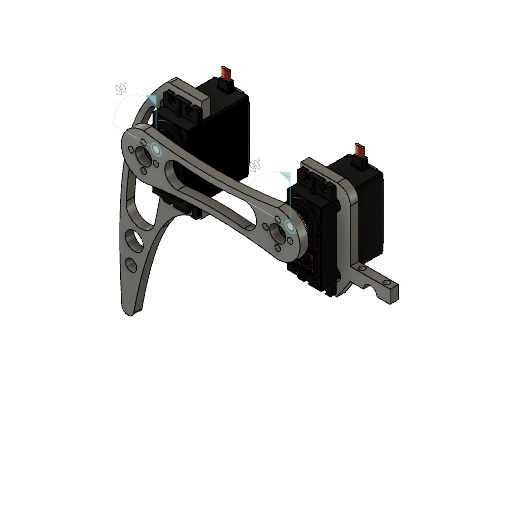
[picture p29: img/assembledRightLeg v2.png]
Right Leg
            </th>
           <figcaption>Fig.1 - Hexbot right leg assembly</figcaption>
        </figure> 
    </td>
    <td align ="left">
       <ol>  
          <li>Put horn on 3 motors.</li>  
          <li>Set the first motor to 90 degrees.</li>  
          <li>Screw the hip onto the first motor's horn.</li>  
          <li>Screw the second motor into the hip motor bracket.</li>  
          <li>Set the second motor to 90 degrees.</li>  
          <li>Screw one end of the upper leg to the horn of the second motor.</li>  
          <li>Set the third motor to 90 degrees.</li>  
          <li>Screw the third motor onto the other end of the upper leg.</li>  
          <li>Screw the lower leg onto the third motor via its motor bracket.</li> 
       </ol>  
    </td>
  </tr>  
</table> 

## Step 2 - Assemble three left legs

Repeat the steps in this section three times in order to create the three left legs that we need. Make note of the orientation of the motors relative to the components that make up the leg in figure 2.

 <table>
  <tr>
    <td align ="left"> 
        <figure>
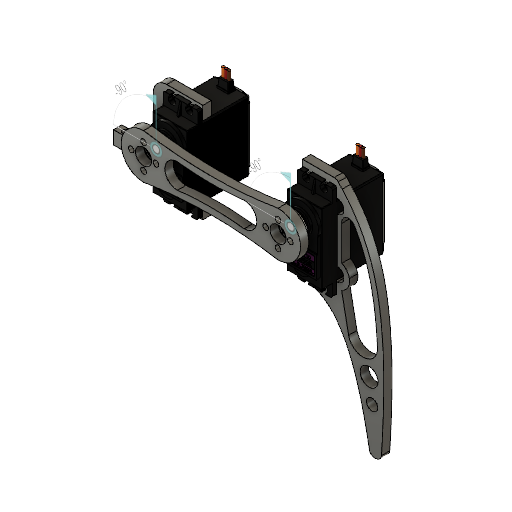
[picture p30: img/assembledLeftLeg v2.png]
Left Leg
            </th>
           <figcaption>Fig.2 - Hexbot left leg assembly</figcaption>
        </figure> 
    </td>
    <td align ="left">
       <ol>  
          <li>Put horn on 3 motors.</li>  
          <li>Set the first motor to 90 degrees.</li>  
          <li>Screw the hip onto the first motor's horn.</li>  
          <li>Screw the second motor into the hip motor bracket.</li>  
          <li>Set the second motor to 90 degrees.</li>  
          <li>Screw one end of the upper leg to the horn of the second motor.</li>  
          <li>Set the third motor to 90 degrees.</li>  
          <li>Screw the third motor onto the other end of the upper leg.</li>  
          <li>Screw the lower leg onto the third motor via its motor bracket.</li> 
       </ol>  
    </td>
  </tr>  
</table> 

## Step 3 - Connect legs to the lower body

Repeat the steps in this section six times in order to attach all six legs to the robot. Make note of the orientation of the motors in figure 3. It is important to ensure that the three motors on each side of the robot body are oriented the same way. When you are done the direction that the servo horns are facing will be considered the front of the robot.

<table>
  <tr>
    <td align ="left"> 
       <figure>
          Full robot assembly 
          <figcaption>Fig.3 - Attaching legs to body</figcaption>
       </figure> 
    </td>
    <td align ="left">
       <ol>  
          <li>Insert a leg assemby into a servo bracket on the body.</li>  
          <li>Use four screws and nuts to secure the assembly in place.</li>  
       </ol> 
       You have now completed assembly of the lower body and legs. Next you need to assemble the electronics platform.
    </td>
  </tr>  
</table> 

## Step 4 - Mount the upper body and electronics

```We are still in the design phase for Hexbot's electronics so this part of the instructions calls for a bit more inginuiuty at present.```

<table>
  <tr>
    <td align ="left"> 
       <figure>
          <img src="/img/topBodyLayer.jpg" alt="top layer" width="500" height="300"> 
          <figcaption>Fig.4 - Top layer</figcaption>
       </figure> 
    </td>
    <td align ="left">
       <ol>  
          <li>Fabricate a 4 3/4" wide by 6 1/2" long rectangle out of a thin light material. A piece of 1/8" plexiglass would work well. We will refer to this as the top body layer.</li>
        <li>Fasten a ~2" by 6" breadboard to the top body layer. Be sure to centre it.</li> 
        <li>Cut the 4 corners of the top body layer off to allow for maximum clearance of the legs.</li>
        <li>Mount 2 motor drivers to the top body layer.</li>
        <li>Drill 1/8" holes in the top body layer. Be sure to align these holes with the nes that already exist in the bottom layer.</li>
        <li>Mount the top body layer to the bottom layer using ~1 1/2" standoffs bolted through the existing mounting holes.</li>
       </ol> 
       Congratulations, you now have a fully assembled Hexbot. From here you need to <a href="/docs/wireMotors.md">wire the motors</a>.
    </td>
  </tr>  
</table>

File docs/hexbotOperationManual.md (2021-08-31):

# Hexbot Operation Manual

This page contains information useful when servicing or operating Hexbot.

## Assembly
Full Hexbot assembly instructions can be found [here](hexbotAssembly.md).

## Code Updates

Code updates can be done in one of two ways. First, they can be done via a local USB micro conection. There are man places to learn how to do this so we will not include instructions here. Code updates can also be updated Over-The-Air (OTA) using Hexbot's web interface. Details on how this is done can be found [here](/docs/hexbotWebInterface.md#ota-updater-screen).

## Configuring NVRAM

Certain environment specific values can be configured in NVRam avoiding the need to rebuild and update code when the robot moves to a new network environment. Full details for this are found [here](/docs/hexbotWebInterface.md#config-updater-screen).

## Data Analytics

Monitoring and dynamic configuration of Hexbot is done via MQTT messages between the web browser client and the robot. The robot outputs two types of data. One is health data in the form of error counts for various events of interest. The second is telemetry data which provides real time sensor data regarding the balancing activities of the robot. The documenation for these messages is maintained within the code itself and is extracted [here]() via Doxygen during merging of code into the main branch of the repository. ```Fix this link once we have Doxygen in place and pull requests automated.```

## Online Documentation

An index of online documentation found in the Hexbot Github repository is located [here](https://github.com/va3wam/hexBot#documentation).

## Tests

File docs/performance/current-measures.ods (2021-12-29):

Servo Count | angle | current
18 | 0 | 0.28
 | 10 | 0.35
 | 20
 | 30
 | 40
 | 50
 | 60
 | 70
 | 80
 | 90

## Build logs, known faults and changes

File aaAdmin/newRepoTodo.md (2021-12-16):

Back to [README](https://github.com/theAgingApprentice/icUnderware/blob/main/README.md)
---

This document contains a 'to do list' of actions to take to start your project using the icUnderware template repository. ```These instructions assume that you have Git installed on your machine and were written using a Mac. It may be that procedures on Windows and Linux machines differ slightly.```

## Process Overview

The following is a brief list of the steps you must take in order to make use of this template repository. Some of the more involved steps include links to a section further down in this document with greater details. 

1. Clone the [icUnderware repository](#Cloning-the-template).
2. Make a [local repo](#Making-a-local-repo).
3. Edit the [Doxyfile](#Editing-the-Doxyfile).
4. Edit the [README.md](#Edit-the-READMEmd-file).
5. Move/rename ```./aaAdmin/platformio.ini.temp``` to ```./platformio.ini```.  
6. Curate the [Github labels](#Curating-the-Github-Labels) in the new repository.
7. [Next steps](#Next-steps).

## Cloning the template

- In your web browser, navigate to the Aging Apprentice template repo [here](https://github.com/theAgingApprentice/icUnderware).
- Click the ```Use this template``` button.
- Follow the online instructions.
- Be sure to click the ```include all branches``` option.
- Invite new contributors if required to do the next steps. 
   - Go to your new Github repo with your browser.  
   - Settings/Manage Access/Invite a collaborator/enter name.
- Click on the ```Code``` button then click on the clipboard icon to copy the URL. 

## Making a local repo

- Get into Visual Studio Code terminal window with no projects open.
- Navigate to the project folder on your local hard drive.
- Issue the command `git clone https://github.com/theAgingApprentice/{project name}` (you can paste the URL that you copied in the previous step)
- Navigate into the newly created directory `cd {project name}`
- Rename **template_platformio.ini_tmp** to **platformio.ini** in the root of your repo.
- Open project in PlatformIO.
   - Start Visual Studio Code. 
   - Start PlatformIO.
- Open project.
## Editing the Doxyfile

There is a file called Doxyfile in the root of the repository. Make the following edits.
- PROJECT_NAME           = {project name}
- PROJECT_BRIEF          = "Brief explanation of what class does."
## Edit the README.md file

Update the README.md file to reflect what your project is all about. 
## Curating the Github Labels

```This process only works on unix systems. A windows script could be made to do this on windows machines```. Github uses [Labels](https://docs.github.com/en/issues/using-labels-and-milestones-to-track-work/managing-labels#about-labels) to provide extra meta data for [Issues](https://docs.github.com/en/issues/tracking-your-work-with-issues/about-issues). It is a good practice to link Issues when merging a branch to main. The default list of Labels that come with a new generic repository are a bit limited. The icUnderware template repository has an easy solution for replacing the standard Labels with a curated list of Labels. In order to use our curated list of Github Labels do the following:

1. Create a Github [personal access Token](https://github.com/settings/tokens). Be sure to select REPO scope. Save the token somewhere safe as you cannot find it again once you close the tab. 
2. Navigate to the aaAdmin directory of the new local repository that you created.   
3. In the bash shell script *updateGithubLabels*, change the targetGithubName value to your Github name.
4. Make sure that the bash script is an executable (chmod u+x updateGithubLabels).
5. Run the script: ./updateGithubLabels taregtRepoName githubPersonalToken 
6. If all goes well you should see 
   - A bunch of messages scroll by in your terminal.
   - In the issues tab of your code repoitory click the Labels button and you should see the curated list of labels. 

# Next steps

Congratulations, you can now start working on your new project! Note that the repository you are using makes use of a number of Github features that you may not be all that familiar with. If you are having trouble getting somethng to work for you check out the [helpful hints](helpfulHints.md) page.

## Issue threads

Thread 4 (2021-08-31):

Addess error initialization from incompatible pointer type [-Wincompatible-pointer-types]

va3wam, 2021-08-31:
https://github.com/va3wam/hexBot/blob/0f974f4970df91e9a6a5f9d082d167453b35ee18/src/main.cpp#L43-L43

va3wam, 2021-08-31:
This error comes up at compile time. It always has a similar message for another line near by:
_**initialization from incompatible pointer type [-Wincompatible-pointer-types]**_. Both of these messages are somehow linked to the file esp32-hal-spi.c.

va3wam, 2021-09-15:
Error has gone now. Got an update to the ESP32 libraries recently which may have addressed this. Closing for now as the issue is gone though we did nothing to address it.

Closed 2021-09-15.

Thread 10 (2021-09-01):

Re-write amI2C library.

va3wam, 2021-09-01:
https://github.com/va3wam/hexBot/blob/b14a6327b650fce4c8ffc3d2039137bf4c722253/include/main.h#L8-L8

va3wam, 2021-09-01:
The current library is named wrong (should have an "aa" prefix). Also it requires that pin definitions be embedded in it. These values should be set by a call so the library is portable. Perhaps passed as arguments at instantiate as well as having methods to reset later..

Closed 2021-09-15.

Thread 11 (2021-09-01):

look into FREERTOS

nerdoug, 2021-09-01:
https://github.com/va3wam/hexBot/blob/b14a6327b650fce4c8ffc3d2039137bf4c722253/src/main.cpp#L44-L44

nerdoug, 2021-12-15:
pre-emptive multitasking would remove a lot of the constraints on how we structure and call routines. There would no longer be a need to "stay out of the way" of the 20 millisecond leg movement task, because it would simply pre-empt what ever else might happen to be running.

theAgingApprentice, 2022-04-17:
Going to drop this issue for now. If we change our minds we can create a new issue.

Closed 2022-04-17.

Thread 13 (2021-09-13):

Make program to line up all motors to ensure that motor home positions are known and consistent.

va3wam, 2021-09-13:
Need a way to get all motors to North position in order to properly assemble the robot's legs at the correct angle. Created the project "pca9685servoExperiments" on Andrew's hard drive to do one motor at a time on row 0 of the 0x40 I2C addressed motor driver.

va3wam, 2021-09-18:
Created a program on my hard drive that puts any servo connected to the PWM pin 15 of the driver with an I2C address of 0x41 to North (300 PWM). Can load this program to calibrate centre of each motor.

Closed 2021-09-18.

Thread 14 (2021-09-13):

Range of motion

va3wam, 2021-09-13:
The full 180 degrees of movement is too much for some of the leg joints. In order to prevent the robot from killing its own motors we are going to need to establish valid ranges of motion for each leg joint.

va3wam, 2021-09-18:
After killing 10 servo motors decided to limit movement to 100 PWM to either side of 300 PWM centre so range is now 200 to 400 PWM.

Closed 2021-09-18.

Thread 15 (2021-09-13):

Current draw of leg motors

va3wam, 2021-09-13:
Some of the motors tripped a reply in my power supply that indicated to me that they were drawing more current and/or voltage than other motors. I think that we should figure out how much current is going to be drawn by the combined leg motors.

nerdoug, 2021-09-13:
I remember measuring the current drawn by the servos, and noting that the
current drawn depends on the position of the servo. I'll see if I can find
those notes, and/or a power supply that makes it easy to measure current.

- Doug Elliott / VA3DAE / ***@***.***

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

nerdoug, 2021-12-15:
assigning to myself. Once I get the servos on my hexbot all working and calibrated, I'll use the SSD command to measure current drawn for various servo positions. (Looks like I need to replace a bunch of servos first.)

nerdoug, 2021-12-18:
should increase the size of the capacitor on the PWM board before doing current measurements.

theAgingApprentice, 2022-01-26:
The capacitors have been upgraded from 470uF to 1000uF and the motors have become more reliable. Closing this issue.

Closed 2022-01-26.

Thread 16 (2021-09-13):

Back-lash in motors

va3wam, 2021-09-13:
There is some back lash in the motors and when moving from east to north and west to north things do not always line up the same. I noticed this on some motors more than others. Not sure that there is much to do here but note that these errors may cause drift in the robots heading when walking over time.

theAgingApprentice, 2021-12-16:
For now we will close this issue for now as we sort out the movement flows. We can re-open this issue later if it becmes a problem.

Closed 2021-12-16.

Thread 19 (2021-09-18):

Figure out how to handle lots of leg movement simultaneously.

va3wam, 2021-09-18:
Use inverse kinematic library to try and control leg movements. Hopefully this will result in simultaneous moves.

nerdoug, 2021-11-30:
The flow approach to leg movement is based on moving each of the 18 servo motors in the legs, essentially at the same time, every 20 milliseconds. There is a challenges with this, because almost all of the leg movement computation is clustered at the 20 msec times.

-the 20 msec task to do the 18 servo changes (which I'll call the frame task (FT) ) needs to run every 20 msec. If other routines are running when the the next FT is due, it will be delayed until the other routines are done, and a check is made to see if it's FT time. Depending how the code in loop() is structured, there could be multiple routines running before the FT check.
To address this:
1) break long running routines into shorter (in terms of worst case execution time) routines that execute sequentially, allowing an FT check between routines
2) structure loop() so that at most 1 routine runs per loop() execution. This ensures the FT check at the start of loop() gets done after every routine execution. This is what we did in TWIPE.
3) use FREERTOS facilities to execute the FT according to a timer, and at a higher priority that other routines. This means that other routines will be paused when the timer expires, while the FT runs. This is the "pre-emptive" part of pre-emptive multitasking.

I'm proceeding to implement steps 1 and 2, with some metrics to see how we're doing at running a consistent 20 msec FT. If that can't be done, we can consider these steps:

a) slightly desynchronize the legs. Doing legs 1, 2 and three in one 20 msec slot, and legs 4, 5, and 6 in the next slot doubles the amount of time available for the leg movements. We could do one leg (3 servos) per 20 msec slot would give more time, and doing one servo per slot is the extreme, but might impact performance
b) start thinking about FREERTOS and pre-emptive multi-tasking.

One factor we'll need to examine, probably via performance metrics, is how much delay is caused by the PWN driver board's processing and I2C bus communications. We may need to make sure the 2 drivers are doing things in parallel as much as possible, and that we minimize using any operations that cause blocking. A last resort approach would be to build our own PWM driver that has a high speed connection to the ESP32, non-blocking communications, and PWM characteristics that are similar to the current board.

nerdoug, 2021-11-30:
one other mitigation if we can't keep up with 20 msec frame changes, would be an effort to optimize the code to reduce execution time. We have deliberately traded off execution speed and procedural efficiency for generality and highly structured data. Moving more towards real time and embedded coding techniques could reduce execution time significantly.

nerdoug, 2021-12-06:
git pull 52 implemented flows for 6 legs, which provides a way to control changing the 18 servos every 20 msec in order to move the legs in a manner described in a "flow". I think this addresses the base question in this issue, although fine tuning may be needed based on performance. closing this issue.

Closed 2021-12-06.

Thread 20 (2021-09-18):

Assemble Doug's robot.

va3wam, 2021-09-18:
Because the way the shin connects to the knee the direction to move the knee up and down is opposite for the left and right legs of the robot. We need to be sure that we coordinate our assembly so that our up and down agree with each other. Not sure of forward and backward are affected that same way at the moment.

nerdoug, 2021-12-15:
discovered that I was using a different convention for leg numbering, which is built in to some software. Will maintain this numbering until my bot is physically stable, and then do current consumption testing which will help Andrew to choose a bench power supply. Once that's done, I'll modify the software to match the original leg numbering scheme.

theAgingApprentice, 2021-12-16:
Switches are not installed but enough is done to allow us to start testing code  etc. Closing this issue.

Closed 2021-12-16.

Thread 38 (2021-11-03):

Nail down universal coordinate values

theAgingApprentice, 2021-11-03:
Decisions:
1. We are going to use a "robot wide" coordinate system.
2. The x axis runs along the spine, the y axis runs across the shoulders, the z axis is up and down.
3. The Robot origin is in the centre of the robot chassis (x,y) and at the same height as the origin of the legs (z).
4. +x is forward. +z is up, +y is his left

To do:
Using Fusion360 create a diagram that shows
1. Angle that the toe on each leg is from the origin x,y
2. The x,y,z home coordinate for each leg toe (home means 0 servo angles)

theAgingApprentice, 2021-11-03:
Home coordinates for each toe are:
Front left leg toe home coordinates: x=+18.63cm, y=+14.82cm,z=-10.56cm
Front right leg toe home coordinates: x=+18.63cm, y=-14.82cm,z=-10.56cm
Mid left leg toe home coordinates: x=0cm, y=+20.80cm,z=-10.56cm
Mid right leg toe home coordinates: x=0cm, y=-20.80cm,z=-10.56cm
Back left leg toe home coordinates: x=-18.63cm, y=+14.82cm,z=-10.56cm
Back right leg toe home coordinates: x=-18.63cm, y=-14.82cm,z=-10.56c

Angles for each leg are:
Front & Back Legs: 38.5d off x axis
Mid Legs: 90d off  x axis

Rough Diagram:
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
m

nerdoug, 2021-11-30:
home position coordinates given here are close to, but not quite the same as those in /docs/hex-coord-translations.ods, sheet "key locations" Not sure if the difference matters.

theAgingApprentice, 2022-04-17:
Moving to a new chassis and new numbers will be published. Can clode this issue.

Closed 2022-04-17.

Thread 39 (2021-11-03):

Rework leg math

va3wam, 2021-11-03:
Switch the X Y and Z axis currently used by the lag math to the new Robot wide coordinate system per issue 38. Translate magic numbers to symbols for robot measurements.

nerdoug, 2021-12-02:
The mathematical complexity of using global coordinates in the leg math is prohibitive. Better (and feasible) to use a local coordinate system that aligns with the orientation of the leg. Supporting this is a routine that converts global coordinates to the local coordinates of a specific leg. Using similar axis names for local and global coordinates can be confusing, so this task will be implemented as reworking the leg math, comments, documentation and variable names to use local axes p, q and r consistently for all legs.

nerdoug, 2021-12-02:
oops. "close with comment" did more closing than I intended

theAgingApprentice, 2022-04-17:
Will be done as part of the reworking of the leg math that will be needed after we get the new chassis.

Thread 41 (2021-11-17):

implement global/local coordinate translation for six legs

nerdoug, 2021-11-17:
Each leg has a different local coordinate system, and associated algorithm to translate the global coordinate system.

nerdoug, 2021-11-24:
see doc file: hex-coord-translations.ods  which has the formulas for global to local coordinates, and a chart showing the global coordinates for each leg's:
-center of hip servo
-local origin
-home position (toe location in neutral stance where all servos are at center position)

Using old local x, y, z axes definitions for now, because it's easy, and there may not be much benefit in reworking it.
Starting to code  translation from global to local coordinates. Don't know if we'll need the opposite translation.

Closed 2021-11-24.

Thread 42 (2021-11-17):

create an MQTT command to move an arbitrary leg to an arbitrary toe location

nerdoug, 2021-11-17:
need to consider checking code to make sure movement is safe - doesn't hit robot, or get too close to an adjacent leg, or get to an area where the leg math is unstable.

nerdoug, 2021-12-07:
checking code for safe toe positions was already implemented for flow processing. Will reuse the code and the same control parameters which specify the dimensions of the safe box around the home position that the toe is allowed to move to. Default values allow toe to move 6 cm away from home position in both directions on all three axes.

command is MOVE_LEG, or ML, case insensitive. Format:

      // command format: ML, f_operation, leg, X, Y, Z
      //  f_operation values:
   const int fo_moveAbs = 1;     // move to absolute location, coords are in global system
   const int fo_moveLocal = 2;   // move to location given, interpreted as local coords
   const int fo_moveRelHome = 3; // move to loc'n relative to home, coords = deltas relative to home position

 = 1 means X, Y, and Z are global coordinates
      //              = 2 means X, Y, and Z are local coordinates

nerdoug, 2021-12-07:
no idea what happened to close this. Still working on the code.

Closed 2021-12-08.

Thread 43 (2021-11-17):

Doug's test issue

nerdoug, 2021-11-17:
Experimental initial issue

<!-- Edit the body of your new issue then click the ✓ "Create Issue" button in the top right of the editor. The first line will be the issue title. Assignees and Labels follow after a blank line. Leave an empty line before beginning the body of the issue. -->

nerdoug, 2021-11-30:
clearing this, which was just for testing.

Closed 2021-11-30.

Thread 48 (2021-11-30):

MQTT commands to bot that are over 32 characters are mishandled, can cause ESP32 crash

nerdoug, 2021-11-30:
Today's merge added an MQTT command FLOW, or FL for short. It defines a row in the arrays that define a flow, and is generally quite long. This individual arguments are described in flow.h . These aren't in the same order as the FLOW command, because the coordinates for a given leg are grouped together, rather than all the X coords that are in the same array. A sample (unrealistic) FLOW command is:
FL,1000,2,10,0,0,0,1,2,3,4,5,6,7,8,9,10,11,12,13,14,15,16,17,18
The numbers from 1 to 18 represent the positions of the 6 toes: 6 legs times 3 coords each = 18 numbers
If you send this MQTT command to the bot, you get this serial monitor output:
==================================================
<onMqttMessage> Received message.
<onMqttMessage>  topic: Hexbot3C61054ADD98/commands
<onMqttMessage>  qos: 0
<onMqttMessage>  dup: 0
<onMqttMessage>  retain: 0
<onMqttMessage>  len: 63
<onMqttMessage>  index: 0
<onMqttMessage>  total: 63
<onMqttMessage>  payload: fl,1000,2,10,0,0,0,1,2,3,4,5,6,7,8,9,10,11,12,13,14,15,16,17,1���␁␁␂␁
<onMqttMessage> Message to process = fl,1000,2,10,0,0,0,1,2,3,4,5,6,7,8,9,10,11,12,13,14,15,16,17,18
<onMqttMessage> msg = fl,1000,2,10,0,0,0,1,2,3,4,5,6,7,8,9,10,11,12,13,14,15,16,17,18
<aaStringQueue::dumpBuffer> Buffer size = 1
<aaStringQueue::dumpBuffer> Lost messages = 0
<aaStringQueue::dumpBuffer> Row 0 = fl,1000,2,10,0,0,0,1,2,3,4,5,6,7,8,9,10,11,12,13,14,15,16,17,18
<aaStringQueue::dumpBuffer> Row 1 = ,2,3,4,5,6,7,8,9,10,11,12,13,14,15,16,17,18
<aaStringQueue::dumpBuffer> Row 2 = 11,12,13,14,15,16,17,18
<aaStringQueue::dumpBuffer> Row 3 = ,18
<aaStringQueue::dumpBuffer> Row 4 =
<aaMqtt::getCmd> Size of string = 925644332
<aaMqtt::getCmd> Command pulled from buffer = fl,1000,2,10,0,0,0,1,2,3,4,5,6,7

Stack smashing protect failure!

abort() was called at PC 0x401418af on core 1

ELF file SHA256: 0000000000000000

Backtrace: 0x40089138:0x3ffb1ea0 0x400893b5:0x3ffb1ec0 0x401418af:0x3ffb1ee0 0x400d693a:0x3ffb1f00 0x400d3dbe:0x3ffb1f40 0x400d423f:0x3ffb1f80 0x400df8e9:0x3ffb1fb0 0x4008a3c6:0x3ffb1fd0

Rebooting...
....
=======================================================
if you reduce the command to:  FL,1000,2,10,0,0,0,1,2,3,4,5,6,7,8,9,10
it doesn't crash, but the command is truncated:
=======================================================
<onMqttMessage> Received message.
<onMqttMessage>  topic: Hexbot3C61054ADD98/commands
<onMqttMessage>  qos: 0
<onMqttMessage>  dup: 0
<onMqttMessage>  retain: 0
<onMqttMessage>  len: 39
<onMqttMessage>  index: 0
<onMqttMessage>  total: 39
<onMqttMessage>  payload: fl,1000,2,10,0,0,0,1,2,3,4,5,6,7,8,9,10'�
<onMqttMessage> Message to process = fl,1000,2,10,0,0,0,1,2,3,4,5,6,7,8,9,10
<onMqttMessage> msg = fl,1000,2,10,0,0,0,1,2,3,4,5,6,7,8,9,10
<aaStringQueue::dumpBuffer> Buffer size = 1
<aaStringQueue::dumpBuffer> Lost messages = 0
<aaStringQueue::dumpBuffer> Row 0 = fl,1000,2,10,0,0,0,1,2,3,4,5,6,7,8,9,10
<aaStringQueue::dumpBuffer> Row 1 = ,2,3,4,5,6,7,8,9,10
<aaStringQueue::dumpBuffer> Row 2 =
<aaStringQueue::dumpBuffer> Row 3 =
<aaStringQueue::dumpBuffer> Row 4 =
<aaMqtt::getCmd> Size of string = 925644332
<aaMqtt::getCmd> Command pulled from buffer = fl,1000,2,10,0,0,0,1,2,3,4,5,6,7
I: <checkMqtt> cmd = fl,1000,2,10,0,0,0,1,2,3,4,5,6,7.
<processCmd>
<aaFormat::aaFormat> Default constructor running.
start processing flow command
<aaFormat::aaFormat> Destructor running.
I: <checkMqtt> All went well.
======================================================
changing to QOS 1 doesn't seem to have any impact.

nerdoug, 2021-11-30:
in lib/aaMqtt-1.00/src/aaMqtt.cpp, in the routine getCmd() there was a line:
       int8_t strSize = cmdQueue.getMaxBufferSize();
int8_t is a signed integer with values from -127 to +127. We're going to need buffers longer than 127. Let's say each of the coords is in the form ",-12.34"  which is 6 characters, time 18 = 128 bytes. Add in the stuff preceding and we're well over a signed 8 bit number. Changed this to an int, but still get the crash. Since the sensitivity seems to be around a 32 byte command length, there's probably some other cause.

nerdoug, 2021-11-30:
Email from Andrew:
I set a maximum size for the command array and I am guessing that this command exceeds it. The problem likely exits on line 45 of aaStringQueue.cpp:

const int8_t COMMAND_MAX_LENGTH = 20;

If I am right then your command is truncated at 20 characters and increasing the value of command_max_len to a larger number will fix the problem

nerdoug, 2021-11-30:
Thought I converted command buf length to 200 characters, and all pointers to INT, but still getting a crash, with aaMqtt::getCmd only seeing the part of command:
<aaMqtt::getCmd> Command pulled from buffer = fl,1000,2,10,0,0,0,1,2,3,4,5,6,7

which happens to be 32 characters long

nerdoug, 2021-11-30:
the output aaMqtt::getCmd Size of string = 925644332  got me looking at aaMqtt.cpp/getCmd().
It looks like it calls cmdQueue.getMaxBufferSize expecting to get the largest number of characters a command can contain.
However, the value returned is BUFFER_MAX_SIZE, which is 5, the number of entries in the queue. The character count is actually in COMMAND_MAX_LENGTH and is currently set to 200.

Think this is the only call, so I'm going to change the routine name to getCmdMaxLength, and have it return COMMAND_MAX_LENGTH. If that doesn't work, I'll bypass the trouble, and use the symbol in aaMqtt/getCmd.

nerdoug, 2021-11-30:
That fixed it. changed getMaxBufferSize();  to getCmdMaxLength() which returns COMMAND_MAX_LENGTH. Got no compile errors, so there were no other calls to getMaxBufferSize(); which has disappeared. New output for same MQTT input:

<onMqttMessage> Received message.
<onMqttMessage>  topic: Hexbot3C61054ADD98/commands
<onMqttMessage>  qos: 1
<onMqttMessage>  dup: 0
<onMqttMessage>  retain: 0
<onMqttMessage>  len: 63
<onMqttMessage>  index: 0
<onMqttMessage>  total: 63
<onMqttMessage>  payload: fl,1000,2,10,0,0,0,1,2,3,4,5,6,7,8,9,10,11,12,13,14,15,16,16,18
<onMqttMessage> Message to process = fl,1000,2,10,0,0,0,1,2,3,4,5,6,7,8,9,10,11,12,13,14,15,16,16,18
<onMqttMessage> msg = fl,1000,2,10,0,0,0,1,2,3,4,5,6,7,8,9,10,11,12,13,14,15,16,16,18
<aaStringQueue::dumpBuffer> Buffer size = 1
<aaStringQueue::dumpBuffer> Lost messages = 0
<aaStringQueue::dumpBuffer> Row 0 = fl,1000,2,10,0,0,0,1,2,3,4,5,6,7,8,9,10,11,12,13,14,15,16,16,18
<aaStringQueue::dumpBuffer> Row 1 =
<aaStringQueue::dumpBuffer> Row 2 =
<aaStringQueue::dumpBuffer> Row 3 =
<aaStringQueue::dumpBuffer> Row 4 =
=========== strSize 200
<aaMqtt::getCmd> Size of string = 200
<aaMqtt::getCmd> Command pulled from buffer = fl,1000,2,10,0,0,0,1,2,3,4,5,6,7,8,9,10,11,12,13,14,15,16,16,18
I: <checkMqtt> cmd = fl,1000,2,10,0,0,0,1,2,3,4,5,6,7,8,9,10,11,12,13,14,15,16,16,18.
<processCmd>
<aaFormat::aaFormat> Default constructor running.
start processing flow command
<aaFormat::aaFormat> Destructor running.
I: <checkMqtt> All went well.

Closed 2021-11-30.

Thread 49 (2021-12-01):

Implement Flows
Assignees: @nerdoug
Labels: enhancement

nerdoug, 2021-12-01:
implement the mqtt commands and loop() driven servo changes to drive leg movements

<!-- Edit the body of your new issue then click the ✓ "Create Issue" button in the top right of the editor. The first line will be the issue title. Assignees and Labels follow after a blank line. Leave an empty line before beginning the body of the issue. -->

nerdoug, 2021-12-03:
flow implementation continues...

Closed 2021-12-06.

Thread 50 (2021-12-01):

review robot measurements

nerdoug, 2021-12-01:
Our measurements for key points on the hexbot's body haven't been 100 percent consistent. Although we don't need a high degree of accuracy, we should make sure we are correct to the nearest .01 centimeter. THe reference used in the software are these arrays, defined in flows.h and populated in flows.cpp/setupFlows.

For completeness, we need to add one more measurement: vertical distance from center of hip servo to the origin.

theAgingApprentice, 2022-04-11:
I believe that this is now taken care of and these values are used in the movement calculations. Leaving for Doug to confirm and close.

theAgingApprentice, 2022-04-17:
Need to re-do once new chassis is built. Awaiting manufacturing process.

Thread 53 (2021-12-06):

constrain leg movements to "safe" locations

nerdoug, 2021-12-06:
There are some possible leg positions (which is the same as saying toe positions) which we want to avoid for one of these reasons:
- it will cause leg to collide with robot body, possibly damaging the leg or the chassis
- it will be in danger of colliding with an adjacent leg, and again, causing damage
- it is in an area where the math supporting leg movements doesn't work for some reason
- it is a place the leg can't possibly reach
- it would require one or more of the servos to rotate more than 90 degrees from the home position

We want to be conservative, and over-restrict the leg movement to be sure we never get close to the situations above.

Two approaches come to mind, each of which analyse the proposed position relative to the home position of the leg (i.e. where the servo motors are all in the center or 0 degrees position).

1) define a "tether" distance which is the maximum distance the toe is allowed to be displaced from the home position. This is the radius of a sphere centred at the home position that includes are the positions considered safe. Although this is easy to compute, it's a pretty crude statement of what's safe.

2) define a "safe box" that encloses the possible safe positions, by using 6 parameters to specify the box. Each of the local coordinate axes would have a maximum allowed positive displacement from the home position, and a maximum allowed negative displacement from the home position.
Here's an example (all using local coordinates):
-local X is distance straight out from the hip
-for the home position, X = 13.78
- we might allow toe to come at most 8 cm towards the body, and no more than 5 cm further away,
   then a position is safe if it's X coordinate is between (13.78 - 8) and (13.78 + 5 ), which is between 5.78 and 18.78

We can define the maximum positive offset from home in the X direction as safeMaxPosX (5 in our example),
and the similar limit in the negative direction as safeMaxNegX (8 in our example, which is a positive number)
To include the other local axes, we would also define
     safeMaxPosY
     safeMaxNegY
     safeMaxPosZ
     safeMaxNegZ

This allow a flexible definition of the safe area, and doesn't impose any symmetry requirements.

It is possible that we might want to change the definitions of the safe box on the fly, for example if the hexbot is pivoting in place. This means that we might need flow parameters to specify this change, which would likely be in the form of a new operation code. But that can be left until later.

I'm implementing a routine called SafeLegCheck which will be called everytime the local coordinates for a new flow row's toe position is calculated (including the special case first row).  We don't need to do this check for every frame. As long as the end points are safe, and the safe box is convex, all points on the line between the endpoints are safe.

nerdoug, 2021-12-07:
delivered in a git pull merge today.

Closed 2021-12-07.

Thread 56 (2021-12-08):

add ToeMoveAction to MOVE_LEG MQTT command
Assignees: @nerdoug
Labels: enhancement

nerdoug, 2021-12-08:
The last argument for the flow_go command controls what is done when hexbot is ready to move toes to the specified new position:
- actually feed the servos a PWM value to do the physical movement
- or, display information like the resulting local toe coords on the serial monitor.

This issue covers providing the same parameter controlled action for the MOVE_LEG command

<!-- Edit the body of your new issue then click the ✓ "Create Issue" button in the top right of the editor. The first line will be the issue title. Assignees and Labels follow after a blank line. Leave an empty line before beginning the body of the issue. -->

nerdoug, 2021-12-18:
while you're at it in this code, add an option to bypass the toe safety box mechanism, so we can carefully test what the movement limits are for each leg.

theAgingApprentice, 2022-04-17:
We are removing this command so we can close this issue.

Closed 2022-04-17.

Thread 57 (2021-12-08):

Add instrumentation to loop() to capture frame timing acuracy

nerdoug, 2021-12-08:
implement gathering metrics on accurately the frame processing is occurring at 20 msec intervals. This may uncover the need to optimize or restructure our code, or to use FREERTOS to get pre-emptive multitasking.

<!-- Edit the body of your new issue then click the ✓ "Create Issue" button in the top right of the editor. The first line will be the issue title. Assignees and Labels follow after a blank line. Leave an empty line before beginning the body of the issue. -->

theAgingApprentice, 2022-04-17:
We still like the idea of being able to do this but we are not aware of any issue that this may be causing. We will keep this as a low priority item.

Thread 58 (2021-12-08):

Investigate current and voltage getting to the motors

theAgingApprentice, 2021-12-08:
Initial voltage readings indicate that not enough power is getting to the motor controller boards.

nerdoug, 2021-12-15:
If we measure battery voltage, servo voltage and servo current, we'll need 3 analog to digital converters. ESP32 has 2 ADC controllers that support 18 ADC channels (with some restrictions) so we should be OK.

nerdoug, 2021-12-15:
I have a number of mini-voltmeter devices that can be hooked up to some of the unused duplicated pins on each PCA9685 to give a real time display of the voltage gong to the servo. Will provide a couple of these to Andrew.
NOTE: These run off the circuit they attach to, and will go blank if the voltage goes below their minimum operating requirement. They handle 4.5 - 5.0 fine, but I have seen them blank out.

theAgingApprentice, 2021-12-16:
Mini-voltage meters added on both bots. Closing issue.

Closed 2021-12-16.

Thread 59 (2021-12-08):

Create MQTT command for testing servo currwnt draw

theAgingApprentice, 2021-12-08:
Create a command that puts Hexbot into a special test mode that allows us to put servos in known positions so that we can take current and voltage measurements. This code is not expected to be long term but is a special test situation to triage power issues that we are seeing (see issue #58 - investigate current and voltage getting to motors) .

nerdoug, 2021-12-09:
Added 3 new MQTT commands:
// SSD command = Set  Servo(s) to angle, expressed in degrees, zero is center of range
   if(cmd == "SSD")     // set servo(s) to degrees
   // command format: SSD, degrees, servo#, (optional end of range servo#)
   //    -90 <= degrees <= 90
   //    1 <= servo# <= 18
   //    servo #1 is hip for leg 1, the front right one

// SSP command - Set Servo(s) to PWM value
   if(cmd == "SSP")     // set servo(s) to PWM value
   // command format: SSP, PWM, servo#, (optional end of range servo#)
   //    110 <= PWM <= 490
   //    1 <= servo# <= 18
   //    servo #1 is hip for leg 1, the front right one

   // SSO command - Set Servo(s) to "OFF"
   if(cmd == "SSO")     // set servo(s) to OFF, where servo goes limp and draws no current
   // command format: SSO, servo#, (optional end of range servo#)
   //    1 <= servo# <= 18
   //    servo #1 is hip for leg 1, the front right one

Code is untested, since my hexbot needs some wiring, but I'm about to do a git merge / pull.

nerdoug, 2021-12-09:
Examples:

set all servos to center position = 0 degrees
   SSD,0,1,18
set all servos on right side to 45 degrees
   SSD,45,1,9
set left side knees to -30 degrees
   SSD,-30,11
   SSD,-30,14
   SSD,-30,17

set all servos on 2 front legs to PWM = 300
   SSP,300,1,3
   SSP,300,10,12

turn off all servos
    SSO,1,18
turn off leg 1's knee servo
    SSO,2

Closed 2021-12-09.

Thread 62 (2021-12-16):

The last servo moves slower than the rest

theAgingApprentice, 2021-12-16:
We have a few theories about what may be happening.

1. The I2C bus' have a contention issue and separating onto different I2C buses will fix this.
2. The PCA9685 cannot handle the number of servos we are using in a timely fashion. To test this change the number of motors we are managing to confirm.
3. The software queue that the PCA9685 always handles the last servo command slower due to how it handles its queue. By dropping and raising the number of servos controlled we could confirm this is what is happening.

nerdoug, 2022-01-12:
resolved in flow processing by:
- changing capacitor on PWM boards from 470 to 1000 micro Farads
- alternating servo commands across PWM boards
- reducing servo movement frame rate from 50 to 20 frames per second.

Some troubleshooting commands such as SSD don't have all these fixes, and may still show last servo misbehaviour.

Closed 2022-01-12.

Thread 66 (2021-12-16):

Issue random twitching of legs with no known changes in environment

nerdoug, 2021-12-16:
When the bot is sitting idle after some sort of servo movement, it will occasionally go into twitching spells, where arbitrary legs make small repeated moves with apparently random timing

<!-- Edit the body of your new issue then click the ✓ "Create Issue" button in the top right of the editor. The first line will be the issue title. Assignees and Labels follow after a blank line. Leave an empty line before beginning the body of the issue. -->

nerdoug, 2021-12-16:
Some possibilities to ponder:
-I2C bus issues
    - pull up resistor issues
    - voltage or current variations
 - some flakey component
 - some flakey wiring

nerdoug, 2021-12-18:
Some troubleshooting techniques:
- increase 5V cap and see if twitching goes away.
- scope the I2C bus to see if there's activity when we're not driving servos, but they're twitching
- similarly, scope the +5 and +3.3 volts lines in various places
- scope various grounds signals, to see if they agree
- might be interesting to scope +5 / Gnd on a servo we're not driving at all.
- see if there's any twitching when only one PWM board is connected. If not, it might be a contention issue
- implement a second I2C bus so activity on both PWM boards can overlap without I2C competition

nerdoug, 2021-12-19:
Haven't seen this twitching (except on initial startup) since increasing the caps on the PWM boards. If this remains the case, I'll close this issue, blaming the caps.

suspect the startup case can be solved by making sure the software sends some command to each servo before the 5V power is enabled, so the servo position isn't undefined when +5V appears. This could be done by the startup software if we put in a relay that controls the 5V power as we considered, and use pullups to ensure it comes up with 5V disabled until a command has been sent to all servos.

theAgingApprentice, 2022-04-11:
I have also noted the issue is much better with new caps.

theAgingApprentice, 2022-04-17:
We put larger capacitors on the controller boards and this seems to have greatly improved the issue. We are now discussing possibly making the caps  even larger to deal with boot up issues but we can consider this issue closed.

Closed 2022-04-17.

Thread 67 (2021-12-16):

Slow down flow logic

theAgingApprentice, 2021-12-16:
Issue seen is that the flow movements are jerky and unpredictable. The suspicion is that this is timing related because when we increased the time interval for the SD commands from 20ms to 30ms the legs became more reliable.

To do:
1. Figure out why extending the SD command from 20ms to 30ms fixed the SD execution.
2. Come up with a plan based on this knowledge to fix the flow executions to make them more reliable.

nerdoug, 2021-12-18:
This may be related to the current surge when a lot of servos move at once, and the standard capacitor that's pre-installed being too small. Opening another issue for capacitor sizing, but it may resolve this one too.

Note that the current amount of delays in the SSD command isn't workable in flows, because there are 18 servos involved in continuous motion, and the delays add up to a total delay that impacts control of the legs.

nerdoug, 2022-01-02:
I have to retract comment that larger delays in grouped servo commands aren't feasible. We could make this work by  increasing the time per frame from current default of 20 msec to something as big as 50 msec, or 20 frames per second. We would still have a cascading leg motion, which is undesirable, but we could have larger delays between servo commands. I think this is more masking the problem than solving the root cause.

nerdoug, 2022-01-12:
jerky leg movements have been resolved by a variety of improvements including:
- soldering connections to PWM boards to avoid vibration induced connection inconsistency
- changing servo movement frame rate from 50 FPS to 20 FPS
- increasing the capacitor on the PWM boards from 470 to 1000 microFarads

There are currently no explicit delays on the flow processing's servo movements. Adding any would be undesirable, because it wastes CPU that can be used for other purposes.

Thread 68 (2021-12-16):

Create "push up" movement.

theAgingApprentice, 2021-12-16:

nerdoug, 2021-12-18:
As a starting point, here a MQTT.fx script I'm testing that moves the hexbot to a squatting position where the toes are 3.5 cm higher than the home position, i.e. the bot's body is 3.5 cm closer to the ground:

	// clear any previous flow
	send("fg,0,0")

	// go to the lying on belly position, with legs 3.5 cm above home position
	// since this is the first flow row, we jump to it directly, then pause for 340 msec
	send("fl,300,3,10,0,0,0, 0,0,3.5, 0,0,3.5, 0,0,3.5, 0,0,3.5, 0,0,3.5, 0,0,3.5")
	//
	// now that we've defined the flow, execute it
	send("fg,1,20,1")          // start er up, 20 msec, move toes and don't print coords for each frame

The arguments of the flow ("fl") command are:
300 - number of milleseconds to execute this move. first position is a special case, and this is ignored
3  - operating mode is relative to home position. numbers given for each leg are toe positions
      expressed as offsets in global X, Y, and Z directions from that leg's home position
10 - we're moving is straight lines between successive flow row toe positions
0,0,0  - parameters that would be used if we were following a parabola or ellipse rather a line between positions
0,0,3.5, - position for leg 1:
                desired X coord is this leg's home position's X coord plus 0
                desired Y coord is this leg's home position's Y coord plus 0
                desired Z coord is this leg's home position's Z coord plus 3.5 cm
0,0,3.5, - position for leg 2, as above for leg 1
0,0,3.5, - position for leg 3, as above for leg 1
0,0,3.5, - position for leg 4, as above for leg 1
0,0,3.5, - position for leg 5, as above for leg 1
0,0,3.5, - position for leg 6, as above for leg 1

nerdoug, 2021-12-18:
Here the full script (untested) for a full push up cycle:

```
var Thread = Java.type("java.lang.Thread");

function execute() {
    out("Hexapod Pushup Test.  File= 01__hexbot-pushup.js");

    myTWIPe = "Hexbot3C61054ADD98/commands"     // Doug's bot
//	myTWIPe = "calServoCC50E394F048/commands"     // Andrew's bot

    out(" ");

	// clear any previous flow
	send("fg,0,0")

	// go to the lying on belly position, with legs 3.5 cm above home position
	// since this is the first flow row, we jump to it directly, then pause for 340 msec
        // note that the safety box for each toe currently limits it to moving at most 6 cm
        //       away from the home position along any axis
	send("fl,300,3,10,0,0,0, 0,0,3.5, 0,0,3.5, 0,0,3.5, 0,0,3.5, 0,0,3.5, 0,0,3.5")
	//
	// go to the neutral or home position, slowly, over 3 seconds. this raises bot 3.5 cm higher
	send("fl,3000,3,10,0,0,0, 0,0,0,  0,0,0, 0,0,0, 0,0,0, 0,0,0, 0,0,0")
	//
	// stretch legs further, to 3.5 cm below the home position. This raises bot another 3.5 cm
	send("fl,3000,3,10,0,0,0, 0,0,-3.5, 0,0,-3.5, 0,0,-3.5, 0,0,-3.5, 0,0,-3.5, 0,0,-3.5")
	//
	// and go back to home position, which lowers the bot by 3 cm
	send("fl,3000,3,10,0,0,0, 0,0,0,  0,0,0, 0,0,0, 0,0,0, 0,0,0, 0,0,0")

	// now that we've defined the flow, execute it
	send("fg,1,20,1")    // start er up, 20 msec, move toes and don't print coords for each frame

    action.setExitCode(0);
    action.setResultText("done.");
    out("Parameter parameter set up complete");
    return action;
}
function send(cmd){
	out(cmd);
	mqttManager.publish(myTWIPe, cmd);
	Thread.sleep(500);
}
function out(message){
     output.print(message);
}
```

nerdoug, 2022-01-13:
the MQTT.fx script 01__hexbot-deep-up-c4.js is a demo pushup script. It does 6 and 3 legged pushups, with increased stability due to pulling the toes 4 cm closer to the center of the bot.

can't attach a .js file, so I'll try zipping it.
[01__hexbot-deep-pu-c4.zip](https://github.com/va3wam/hexBot/files/7860052/01__hexbot-deep-pu-c4.zip)

Closed 2022-01-13.

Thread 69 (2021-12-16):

investigate leg movement for (0,3.5,0) case. should be towards body on one side, and away on other

nerdoug, 2021-12-16:
using a positive offset in the global coord system for the global y coord should always move leg towards the global +y direction. In a test we saw all legs move towards the robots body in this case.

<!-- Edit the body of your new issue then click the ✓ "Create Issue" button in the top right of the editor. The first line will be the issue title. Assignees and Labels follow after a blank line. Leave an empty line before beginning the body of the issue. -->

nerdoug, 2021-12-18:
found a bug in the routine that translates global coordinates. The bug only affects legs 4 and 6 (using Doug's leg numbering) and has been fixed in branch "debug" but not merged yet

nerdoug, 2022-01-12:
final resolution involved fixes to conversion routine from local coordinates to servo angles.

Closed 2022-01-12.

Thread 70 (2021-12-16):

Review movement algorithm for legs on opposite sides of body.

theAgingApprentice, 2021-12-16:

theAgingApprentice, 2021-12-16:
For now we are using flows to figure out movements. If/when we decide we want  canned movements we can revisit this issue.

Closed 2021-12-16.

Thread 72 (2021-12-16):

Create lean forward and backward movement.

theAgingApprentice, 2021-12-16:

theAgingApprentice, 2021-12-16:
For now we are using flows to figure out movements. If/when we decide we want  canned movements we can revisit this issue.

Closed 2021-12-16.

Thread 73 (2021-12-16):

Create lean left and right movement.

theAgingApprentice, 2021-12-16:

theAgingApprentice, 2021-12-16:
For now we are using flows to figure out movements. If/when we decide we want  canned movements we can revisit this issue.

Closed 2021-12-16.

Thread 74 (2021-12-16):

Determine max movement for leg joints

theAgingApprentice, 2021-12-16:

nerdoug, 2021-12-18:
I haven't tested the new MOVE_LEG command, but once I do, it will be a way to determine the limits for each leg. Will probably need a special mode that bypasses the toe safety box mechanism so it doesn't keep the toe from getting close to boundary conditions we're looking for.

Still need a healthy safety margin to take imperfectly calibrated servo horn positions into account.

nerdoug, 2022-02-01:
There are a couple of constraints on leg movements:
-limits imposed by servo motor hardware. I think we're assuming plus and minus 90 degrees from center position, even though specs may allow more
-limits imposed by needing to avoid leg parts colliding with robot body. This can be determined by doing a lot of careful testing. The result is a set of pre-determined restrictions that don't change at run time
-limits imposed by needing to avoid hitting adjacent legs. This can be approximated by a conservative volume of allowable toe positions for each leg, but this sacrifices some safe movements. The toe safety box that's already implemented follows this approach, and is pre-determined and doesn't change at run time. A more ideal situation would be to track adjacent leg positions, and allow any movement that did not put any of the moving leg's parts within a settable safe distance from any part of either adjacent leg. This is NOT pre-determined, and must be done at run time.

theAgingApprentice, 2022-04-17:
Do this once we move to the HiTec servo motors. Rough centre is 300 PWM. Will account for fine adjustments in software with newer code that we have planned.

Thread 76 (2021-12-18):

A flow with only an initial position for legs goes into a loop

nerdoug, 2021-12-18:
Usually, you run out of flow rows after doing at least one set of "lines" between 2 flow rows. There's a special case where there's only one flow row, and you run out of flow rows in the flow initialization code for the first row. This case was being recognized, but the flow processing wasn't being stopped by setting f_flowing to false. fixed in branch debug

<!-- Edit the body of your new issue then click the ✓ "Create Issue" button in the top right of the editor. The first line will be the issue title. Assignees and Labels follow after a blank line. Leave an empty line before beginning the body of the issue. -->

nerdoug, 2022-01-01:
this is fixed in code that is part of a git pull

Closed 2022-01-01.

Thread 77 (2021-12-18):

PWM board capacitors may be too small

nerdoug, 2021-12-18:
When you move a lot of servos at the same time, there is a sudden demand for current on the 5V supply line. There are a bunch of factors that impact whether or not this surge demand can be met, including the attributes of the power supply, and the resistance, impedance and capacitance of the circuitry.

The ideal solution is a capacitor located very close to the devices needing the current which stores charge and can make up any temporary shortages.

I ran across a "hooking it up" document for the PCA9685
    [https://learn.adafruit.com/16-channel-pwm-servo-driver/hooking-it-up](https://learn.adafruit.com/16-channel-pwm-servo-driver/hooking-it-up)

----------- which has this to say:
Adding a Capacitor to the thru-hole capacitor slot

We have a spot on the PCB for soldering in an electrolytic capacitor. Based on your usage, you may or may not need a capacitor. If you are driving a lot of servos from a power supply that dips a lot when the servos move, n * 100uF where n is the number of servos is a good place to start - eg 470uF or more for 5 servos. Since its so dependent on servo current draw, the torque on each motor, and what power supply, there is no "one magic capacitor value" we can suggest which is why we don't include a capacitor in the kit.
------------ end of quote

We have 9 servos on each PWM board, so the n * 100uF starting point would be 900uF. I'd be tempted to go a little higher, because we are definitely hitting the worst case of trying to drive all of the servos at the same time. The 470uF one that came on the board definitely seems to small, and this could account for several of the symptoms we've seen.

I have fresh 1000uF electrolytic caps that are the same diameter as the ones that come on the board, but 50% taller. I think I'll measure a couple of them, and swap in the ones with the highest capacitance.

nerdoug, 2021-12-19:
changing capacitors to 1000uF has improved performance significantly. No twitch observed since this change, and all motors are responding consistently. Next step is to reduce the delays after each servo is moved in the SSD command, and see if it still works reliably, and if the cascading motion comes closer to simultaneous.

nerdoug, 2022-01-02:
this is a confirmed performance improvement. closing issue

Closed 2022-01-02.

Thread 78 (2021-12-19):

Doing a flow to home position puts ankle at 3.1 degrees

nerdoug, 2021-12-19:
executing a flow to an offset of (0,0,0) from the home position, should put all servos to an angle of zero' hip and knee are very close to zero, but ankle is3.13 or 3.06 degrees, depending on the leg, based on debug output.

You can also see the legs (ankles only, actually) move slightly if you do a flow to the home position, and then do a SSD to 0 for all servos. These should be the same position, and there shouldn't be any movement

<!-- Edit the body of your new issue then click the ✓ "Create Issue" button in the top right of the editor. The first line will be the issue title. Assignees and Labels follow after a blank line. Leave an empty line before beginning the body of the issue. -->

nerdoug, 2022-01-12:
resolved by corrections to routing that does conversion from local coordinates to servo angles, and more accurate measurements of hexbot leg parts.

Closed 2022-01-12.

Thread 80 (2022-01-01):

Don't move servos if the delta movement is zero

nerdoug, 2022-01-01:
For a lot of leg movements, at least one servo does not move. For example, in a "pushup" the hip servos stay at the same position. However, the current code still goes through all the motions of moving these servos to"updated" positions, which are in fact all the same. Avoiding these redundant servo moves would reduce the use of some critical resources: PWM board processing, I2C bus tme and contention, and well as ESP32 cpu usage.

The deltas we currently calculate are for movement in the local x,y and z directions, and a zero does not necessarily mean a zero delta for servo movement. We probably need to track the 18 servo angles to be able to tell, for each one, if the next angle position is the same as the previous one, and can therefore be skipped.

<!-- Edit the body of your new issue then click the ✓ "Create Issue" button in the top right of the editor. The first line will be the issue title. Assignees and Labels follow after a blank line. Leave an empty line before beginning the body of the issue. -->

nerdoug, 2022-01-01:
must put in a milestone in order for issued assign to me to appear in the VSC/Git/My Issues  list.

nerdoug, 2022-01-12:
implemented in latest code. Last servo angles are remembered in f_lastAngH[L], and servo commands are only generated if the new angle is different:
````
{  if(f_angH != f_lastAngH[L])               // if new hip angle is different than last one, move the servo
   {  pwmDriver[legIndexDriver[L]].setPWM(legIndexHipPin[L],  pwmClkStart, mapDegToPWM(t_angH,0));
      f_lastAngH[L] = f_angH;                // and update last angle for this servo
   }
}
````
note that these are the geometric angles, not the temporary ones that may be negated due to the different physical mounting of the servos on either side of the robot.

Closed 2022-01-12.

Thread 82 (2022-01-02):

Alternate servo command across PWM controllers

nerdoug, 2022-01-02:
The current implementation does the servo movements in each leg, in leg order: L1H, L1K, L1A, L2H, L2K...
This means that the first 9 servo movements all go to the same PWM controller. If we alternated the controllers, each would have some recovery time while the other one was being used.

Two possible orders come to mind:
L1H, L1K, L1A, L4H, L4K, L4A, L2H, L2K ... This would be easy to implement, because the calculations for movements are done "one leg at a time". The change would just be a simple re-ordering of existing procedures. There's also an opportunity to put a delay at the end of each leg, to let I2C bus activity settle.

L1H, L4H, L1K, L4K, L1A, L4A, L2H ... This would require restructuring the existing code. Could use existing code to build a table of new positioning commands, and then perform the actual commands in whatever order is desirable. Since only the command execution has critical timing, the calculations could be lowered in priority, and it might even be possible to do the actual commands at interrupt level.
You might be able to detect when the I2C bus goes idle, and wait until that point to issue the next command

If the 2 PWM controllers were on separate I2C busses, alternating them might further reduce I2C contention.

nerdoug, 2022-01-12:
This is implemented in the flow processing command via a nested for loop:
```
         for(int l_base=1;l_base<=3;l_base++)   // use alternate sides for leg movements, resting PWM drivers
         {  for(L=l_base;L<=l_base+3;L=L+3)     // i.e. 1, 4, 2, 5, 3, 6 
            {                                   // use frame count to figure next frame position
```
It seems to have resolved the problems with the last servo command being lost occasionally. There are no DELAY commands between servo commands in flow processing.

Closed 2022-01-12.

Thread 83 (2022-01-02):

increase default msecPerFrame from 20 to 50 msec

nerdoug, 2022-01-02:
The servo movements for each of the rows in a flow are divided into frames. A standard time per frame interval is used to calculate how many frames are needed to achieve the movement in the time duration specified in the flow row.
The variable that controls this is f_msecPerFrame, which defaults to 20. This is equivalent to 50 servo repositions per second, which seems like overkill, when compared to 24 FPS video. 50 msec, or 20 FPS seems realistic, and gives a lot more headroom for the software to prepare for the next servo movement. It would also allow the insertion of longer delays between individual servo commands if that is needed to achieve reliable and consistent leg movement, although this seems to cause a visible cascading of leg movement.

nerdoug, 2022-01-12:
This behaviour is already parameter controlled, via flows.cpp/msecPerFrame and f_msecPerFrameDefault. No code changes needed, and flows seem to execute fine at 20 frames per second = 50 msec per frame.
closing issue.

Closed 2022-01-12.

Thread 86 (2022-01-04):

Move_Leg cmd doesn't account for reversed mounting of knee and ankle servos on left and right side of robot

nerdoug, 2022-01-04:
The conversion of a knee or ankle angle, in degrees, to a PWM value suitable for feeding to a servo is complicated by the fact that the knee and ankle servos are mounted differently on either side of the bot. Using Doug's leg numbering, the angles need to be negated before PWM conversion on legs 4, 5 and 6. This does not apply to the hip servo.

theAgingApprentice, 2022-04-17:
Getting rig of move leg command so we can close this issue.

Closed 2022-04-17.

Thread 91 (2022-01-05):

leg angle experiment

nerdoug, 2022-01-05:
try different compensations for servo mounting variations

nerdoug, 2022-01-12:
The original approach of reversing the PWM directions for the left side, legs 4, 5 and 6( Doug's numbering) due to the physical mounting of the servos was correct. The apparent splay of the legs in a 3 legged pushup was due to flexing of the legs and servos under the strain. Leg 2 carries more of the load in a 3 legged pushup with legs 2,4 and 6, so it flexed more. This approach is mitigated by drawing the toes closer to the chassis in this operation, reducing the torque load on the knee and ankle servos. Pulling them in 2 cm was a visible improvement, and an additional 2 cm will be tested.

The topic of this issue has been resolved in code I'm about to upload to github, so I'm closing this issue

nerdoug, 2022-01-13:
pulling legs in a total of 4 cm (see script 01__hexbot-deep-pu-c4.js) seemed to improve things, but it's pretty subjective.

Closed 2022-01-12.

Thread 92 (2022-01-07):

rewrite MQTT MOVE_LEG command, which has been disabled

nerdoug, 2022-01-07:
```
   // todo
```

https://github.com/va3wam/hexBot/blob/6a981e96352f3115a41f6d7aa0a0d8ca7432f8c7/include/mqttBroker.cpp#L440

nerdoug, 2022-01-07:
if (cmd == "MOVE_LEGx" || cmd == "MLx")   // the "x" additions effectively disable this command
   { // command format: ML, f_operation, leg, X, Y, Z
   // *************************** this command needs to be reworked to:
   // todo #92
   // allow all movement methods used in flow rows
   // use changed format of globCoordsToLocal routine

see issue 86 as well.

theAgingApprentice, 2022-04-17:
We have decided to remove this code (which is commented out anyhow) and not bother trying to fix it as we never use it anyhow.

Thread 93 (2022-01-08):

flows.cpp/anglesTo Coords() has math error in toeX caclulation

nerdoug, 2022-01-08:
```
   // todo
```

https://github.com/va3wam/hexBot/blob/a2c231bf53be29316aa9b9b8a84dc98809524783/include/flows.cpp#L103

nerdoug, 2022-01-08:
the overall multiplication by cos(radians(hip) at the end of the line is intended to convert the toe x coord in the rotated xy plane to a valid x coordinate without the rotation. This should be done with the formula for rotation of a 2D vector, not a simple trig function.

I don't think this routine is actually called from anywhere. It was included for completeness in the original set of inverse kinematics routines.

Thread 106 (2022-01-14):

Mount battery, power and reset buttons to Andrew's robot

theAgingApprentice, 2022-01-14:

theAgingApprentice, 2022-01-26:
A third level added with the battery and control interface on it. Clsing issue.

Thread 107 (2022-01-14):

Mount battery, power and reset buttons to Doug's robot

theAgingApprentice, 2022-01-14:
Andrew has cooked up a possible mounting solution involving long M3 fine threaded rod and a third platter that holds the buttons and battery mounting hardware.

theAgingApprentice, 2022-04-17:
Waiting until next version of the robot chassis is ready.

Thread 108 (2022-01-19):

[E][WebServer.cpp:633] _handleRequest(): request handler not found

theAgingApprentice, 2022-01-19:
This error comes up from time to time in console traces. It is not clear what the implications of this message are as everything seems to be working just fine.  This message seems relatively new  meaning that the work being done with the MQTT messaging scripts may be somehow related even though this seems  to be more specific to the web service.

theAgingApprentice, 2022-04-17:
Problem  was resolved with new drop of VSC.

Closed 2022-04-17.

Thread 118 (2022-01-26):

Add ability to turn off 5VDC power to motor controllers

theAgingApprentice, 2022-01-26:
Be able to turn the power to the motor controllers on and off from the ESP32 SOC.

theAgingApprentice, 2022-04-10:
I have been thinking about the power control for our servo motor controllers I think we can very easily control the 3.3 and 5.0 VDC voltages for the PCA96856 servo drivers using a couple of Logic Level Enhancement-Type N-Channel MOSFET transistors.

What I think that we need
1. A MOSFET with a Vgs of 3 VDC (or less) so that the ESP32 can turn it on and off.
2. We are only using this as an on/off switch, not PWM, so the rise and fall time characteristics are not that important to us.
3. We want a transistor that is comfortable working at a constant current of say 3 AMPS
4. We think that peak current could be 18 AMPs

Type of MOSFET
Check out this article: https://circuitjournal.com/which-mosfet-should-you-use-with-arduino
We can pull the pin low to a comma ground to ensure no floating problems and that the gate is closed at boot up.

Which MOSFET
According to this article: https://www.instructables.com/ESP32-and-DC-Motors-Tutorial-Part-1/, theRFP30N06LE MOSFET (spec sheet: https://www.sparkfun.com/datasheets/Components/General/RFP30N06LE.pdf) can be driven by an ESP32.

Where to buy
A pack of 5 of these can be purchased on Amazon Canada for $11.00 ([https://www.amazon.ca/Gikfun-RFP30N06LE-N-Channel-Mosfet-Arduino/dp/B01GNORMWA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](https://www.amazon.ca/Gikfun-RFP30N06LE-N-Channel-Mosfet-Arduino/dp/B01GNORMWA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,aps,175&sr=8-1-spons&psc=1&spLa=ZW5jcnlwdGVkUXVhbGlmaWVyPUEyVERDWkY4MEVIRkJQJmVuY3J5cHRlZElkPUEwNTUxNDkzMzVEUlFWSUdIWlowTyZlbmNyeXB0ZWRBZElkPUEwNDQ5MzE1M1VFRjFWSDBXMUNVNCZ3aWRnZXROYW1lPXNwX2F0ZiZhY3Rpb249Y2xpY2tSZWRpcmVjdCZkb05vdExvZ0NsaWNrPXRydWU=))

If you are up for it check my thinking and let me know if you feel that these are worth purchasing.

theAgingApprentice, 2022-04-10:
Issue #157 covers this topic and this is really just a duplication. Closing.

Closed 2022-04-10.

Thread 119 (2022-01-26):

Monitor the current and voltage to the motor controllers

theAgingApprentice, 2022-01-26:
Be able to monitor the current and voltage going to the motor controllers. This will allow us to power down when their are strange spikes in the current.

theAgingApprentice, 2022-04-17:
We are debating if we should do this. Very nice to have but may not be practical to implement.

nerdoug, 2022-05-30:
We've decided we need to do this in order to have reliable startup of the servos. Since this is included in issue 157, I'm closing this one.

Closed 2022-05-30.

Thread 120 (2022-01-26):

Seperate motor and CPU 5VDC power

theAgingApprentice, 2022-01-26:
Isolate the power going to the motor controllers from the battery from the power going to the ESP32 SOC from the battery to prevent back EMF from damaging the micro controller.

theAgingApprentice, 2022-04-17:
Closing as duplicate.

Closed 2022-04-17.

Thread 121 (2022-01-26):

Sometimes legs go limp

theAgingApprentice, 2022-01-26:
On a fairly regular basis one or more legs can go limp during the development of flows. It may be that hand moving the joints contributes to this issue. When this happens it seems that a series of power cycling of the motor controllers eventually solves the problem. We need to sort out why this happens and  prevent it from occurring in order for the robot to be reliable.

theAgingApprentice, 2022-04-11:
Doug is currently investigating this issue which we believe is tied to the way the servo motor controller is powered up. We have a separate ticket to track the the design of that circuit.

theAgingApprentice, 2022-04-11:
That other ticket is #120

theAgingApprentice, 2022-04-17:
Duplicate issue. Closing.

Closed 2022-04-17.

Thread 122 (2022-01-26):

Motors can lock up for no apparent reason

theAgingApprentice, 2022-01-26:
It has been noted that sometimes some of the servo motors lock up so that even when there is no power they cannot be moved by hand. This seems to happen most often to the hip motors. It seems that when power is applied the motors behave fine but we should still figure out what is causing this.

nerdoug, 2022-02-01:
Doug has never observed this, although it may have happened and not been detected.

theAgingApprentice, 2022-04-11:
Andrew is the only one who has seen this. We think that this is also tied to the power up sequence which is being tracked in a different ticket.

theAgingApprentice, 2022-04-11:
That other ticket is #120

theAgingApprentice, 2022-04-17:
Duplicate issue. Closing.

Closed 2022-04-17.

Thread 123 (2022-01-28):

Fix wiring diagram

theAgingApprentice, 2022-01-28:
The wiring diagram shows the v+ pin on the PCA9685 servo motor controller going to 3.3VDC but it should go to 5.0VDC.

Closed 2022-01-28.

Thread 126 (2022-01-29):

need to write a document on how to create a flow scriptIssue Title

nerdoug, 2022-01-29:
We need a document that describes how to write a flow script, including all field definitions in the 2 flavours of the MQTT flow command, and the 2 flavours of the FLOW_GO vommand, and the method for defining and calling repeated cycles of multiple flow rows.

This will also provide input into what the flow compiler needs to produce as it's MQTT script output

nerdoug, 2022-02-01:
needs to cover:
-initial flow go command to reset flow environment
-final flow go command, and all the options
-repeatable cycle commands
-convention to number flow rows in comments for reference
-all of the f_operation functions
    - absolute coords vs. relative to home vs. relative to last
    - global coords vs local coords
-how to graph leg positions for all or part of a flow
-how to get a nicely formatted display of a flow
-how to work with MQTT.fx
    - restart if you create a new script file,
    - minimum delay of 200 msec between commands.
    - file naming conventions
    - identifying target hexbot

nerdoug, 2022-02-06:
This completed document was just uploaded/merged: creating-flows.odt along with a sample script onestep. Submission was done under issue 133. closing this issue

Closed 2022-02-06.

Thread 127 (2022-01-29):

create a script that shows how flow cycles workIssue Title

nerdoug, 2022-01-29:
write a documented script that uses the new repeatable cycle feature  that can be used as a reference

<!-- Edit the body of your new issue then click the ✓ "Create Issue" button in the top right of the editor. The first line will be the issue title. Assignees and Labels follow after a blank line. Leave an empty line before beginning the body of the issue. -->

nerdoug, 2022-01-29:
the file ...docs/MQTT scripts/rotation has a new file 01__hexbot-drotate-cycles.js  which is a re-implementation of 01__hexbot-drotate12.js using cycles rather than cut and paste copies of the basic sequence. It is documented via comment lines.

Closed 2022-01-29.

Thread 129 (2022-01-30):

create optional graphable toe position output controlled by FG command at end of script

nerdoug, 2022-01-30:
add an extra bit to toeMoveAction parameter in the FG command that ends an MQTT flow script to enable graphable output.
This output is generated every time the toes are moved and uses global coordinates in a format that can be used in Excel scatter graphs to make a top view picture of the successive toe positions.

To support this, add a coordinate translation routine flows.cpp/void localCoordsToGlobal(int legNumber, float lx, float ly, float lz)

There's a trick to doing multiple scatter graphs in one chart. See: https://ask.libreoffice.org/t/multiple-scatter-plots/2234

Also need to document the process to create a graphed flow.

<!-- Edit the body of your new issue then click the ✓ "Create Issue" button in the top right of the editor. The first line will be the issue title. Assignees and Labels follow after a blank line. Leave an empty line before beginning the body of the issue. -->

Closed 2022-01-31.

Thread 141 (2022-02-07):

Document VSC procedure to do a safe Github merge

nerdoug, 2022-02-07:
When multiple people are doing concurrent development, you need to make sure your origin merges use the latest code, and not the snapshot you took when you started your branch.

We have procedures documented to do this using the a combination of the Github browser interface and a terminal console:
      https://va3wam.github.io/versionControl/
but not one within the VSC environment, which has become our standard.

According to a website I found:
   BEFORE VS Code 1.48, VS Code Source Control has no UI for merging branches.
   reference: https://code.visualstudio.com/updates/v1_48#_git-overflow-menu-cleanup

However you can now do this, and I think the following steps are equivalent:

- make sure all the changes in your branch are staged and committed locally
- depending on your confidence level and experience with git, make backups of your changed source files
- click on branch name at bottom left of VSC window, and checkout the local main or master branch
- in source control, click the ellipsis at the top, then on "pull" on the resulting popup
- click on the branch name (main or master) in the bottom left and select your branch
- in source control, click the ellipsis, then on "checkout to", then your branch name
- in source control, click the ellipsis, then "Branch" then "Merge Branch", then main or master
- ( we could push the updated branch to origin, but that will be done for us as part of Pull Request)
- in source control, click the complicated icon to the right of the check mark to initiate a pull request
- enter a brief description, and click on the blue "Create" button
- you may get a message saying there's no upstream branch mirroring yours. That's because we were too lazy to publish above. Click the "Publish branch" button to have it done for you.
- A Pull Request form will appear at the top of the right VSC pane. If the "Close Pull Request" button isn't visible at the bottom, lower the pane boundary until you can see it all.
- ideally, the branch has no conflicts with the base branch. Otherwise, you need to fix that first.
- add comments in the "Leave a comment" box near the bottom if you wish
- click on the blue "Merge Pull Request" button
- click on the blue "Create Merge Commit" button
- click on the "Delete branch..." button
- at the top, click the blue "OK" to clean up both local and remote copies of the branch
- close the Pull request window
- in the bottom left corner, click the circle-with-arrows icon just to the right of "main" or "master", which will update the copy on your PC
- click OK on the popup window warning that this will push and pull commits
- if you're prone to making source changes before you create a branch, prevent that by opening a "I won't use this" branch now,
    which you can delete when you remember to open a branch properly. I call these "safety-n".
- if you're sceptical, use your browser to go to git and verify that your changes are there

I have used the above procedure successfully.

nerdoug, 2022-02-09:
guess we need to do overlapping Github uploads to test this before I can close the ticket.

va3wam, 2022-02-09:
OK, we can do that when we meet up own Sunday.  You seem to be making great progress on all of this!

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

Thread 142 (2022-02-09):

rename flow_go commands to something more intuitive

nerdoug, 2022-02-09:
The 2 variations of the FLOW_GO command that start and end a flow script are confusing, and more complicated then they need to be. Need to implement improved names, and update the help command and the creating-fows documentation

<!-- Edit the body of your new issue then click the ✓ "Create Issue" button in the top right of the editor. The first line will be the issue title. Assignees and Labels follow after a blank line. Leave an empty line before beginning the body of the issue. -->

nerdoug, 2022-02-09:
how about replacing FLOWGO, 0, 0   with NEW_FLOW  , shortform NF, with the syntax being just the command for now

replace FLOW_GO,1,msecPerFrame, toe-action   with DO_FLOW , shortform DF.

Syntax: DF, toe-action, msecPerFrame
changing the order lets you leave out the msecPerFRame,  to specify a toe-action and the default msecPerFRame value.

nerdoug, 2022-02-09:
Also need to modify all existing scripts to use the new commands and syntax

Closed 2022-02-09.

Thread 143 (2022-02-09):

add flow command to temporarily redefine the local home coordinates

nerdoug, 2022-02-09:
Sometimes, the leg activity is based on a location other than the pre-defined local home position. For example, for stability, you might want to pull all legs back 4 cm along the local X axis to get them more under the robot. In effect, this becomes the new home location.
If we make this the new home, then the move operations that are relative to home will be based on this location instead, which could simplify the coding of flow commands.

Current plan:
implement new f_operation value   fo_newHome
- needs to be consecutive with cycle op-codes for short/long form flow command checking
- one to four arguments
      f_nhCodeCurrent = 0;    //  use current leg location as temporary home
      f_nhCodeDefault = 1;    // revert to original home position (-13.78, -10.6, 0)
      f_nhCodeGiven = 2;      // use new 3 flow command parameters as the local home position x, y, and z
                                            //   ... this removes the need to move leg to the position before making it home
- need to update creating-flows document
- need to reset local home in fg,0,0 = NEW_FLOW command
- need new data structures to hold temporary home? (depends on coding)
- need to modify code for some move operation codes? ( maybe, maybe not)

nerdoug, 2022-02-09:
The desired home position may not be the same for all 6 legs. This means that the home position needs to be represented by x, y and z arrays that hold a value for each of 6 legs. It also means that specifying a new home location with explicit coordinates needs 18 numbers, not the 3 shown above for the f_nhCodeGiven option of the fo_newHome operation. Could put the coordinates in the flow command, but then the fo_newHome operation would have both long and short versions.

Maybe use different operations codes for
f_nhCodeCurrent = 0; // use current leg location as temporary home
f_nhCodeDefault = 1; // revert to original home position (-13.78, -10.6, 0)
f_nhCodeGiven = 2; //

so the argument count handling is done at the operation code level. These would all need to be treated like the cycle commands on procNextLine(), since they are overhead commands that don't actually get the information needed for the next set of leg movements.

ordering of F_operation codes:

-basic move commands, absolute vs relative to home / global or local
- ---- end of commands that prepare for next line, start of overhead commands (cycles, newhome, toesafety)
- newHome with specified (global/local) coordinates in 18 numbers
- ---- end of commands with 18 numbers, start of short commands
- newHome using current location
- newHome using original home positions
- toeSafety-X
- toeSafety-Y
- toeSafety-Z
- toeSafetyReset

nerdoug, 2022-02-09:
git reformatted last entry on me. At the end, the basic move commands should be the first entry in the list of f_operation codes

nerdoug, 2022-02-09:
last on the list should have been the cycle related short form commands:
   const int fo_markCycleStart=9;  // note this flow row number as the beginning of a numbered cycle within the flow
   const int fo_markCycleEnd =10;  // note this flow row number as the end of a numbered cycle within the flow
   const int fo_doCycle = 11;  // execute the specified cycle for the specified number of iterations.

It's getting confusing - see ...include/flows.h/f_operation[flowlength]. The f_operation codes are defined right after that line.

nerdoug, 2022-02-09:
```
int f_operation[flowLength];        // type of operation specified for this position
   const int fo_moveAbs = 1;        // move to absolute location, coords are in global system
   const int fo_moveLocal = 2;      // move to location given in local coords
   const int fo_moveGRelHome = 3;   // move to loc'n relative to home, coords = GLOBAL deltas relative to home position
   const int fo_moveLRelHome = 4;   // move to loc'n relative to home, coords = LOCAL deltas relative to home position
   const int fo_moveGRelLast = 5;   // move to loc'n relative to last position, coords = global deltas w.r.t. last position
   const int fo_moveLRelLast = 6;   // move to loc'n relative to last position, coords = local deltas w.r.t. last position
// end of operations that that prepare coordinates for next leg movement, start of control commands
   const int fo_newHomeGCoords = 20;// redefine home position using 18 global coords in this command
   const int fo_newHomeLCoords = 21;// redefine home position using 18 local coords in this command
// ---- end of long form commands containing 18 numbers
   const int fo_newHomeHere = 41;   // define new homes for all legs at their current positions
   const int fo_newHomeReset = 42;  // go back to original home position definitions for all legs
   const int fo_ContinuePrev = 43;  // start flow with next move, treating end of last flow as previous position
   const int fo_markCycleStart=50;  // note this flow row number as the beginning of a numbered cycle within the flow
   const int fo_markCycleEnd = 51;  // note this flow row number as the end of a numbered cycle within the flow
   const int fo_doCycle = 52;       // execute the specified cycle for the specified number of iterations.
   const int fo_toeSafetyX = 60;    // specify new plus and minus safety limits for local X coordinate
   const int fo_toeSafetyY = 61;    // specify new plus and minus safety limits for local Y coordinate
   const int fo_toeSafetyZ = 62;    // specify new plus and minus safety limits for local Z coordinate
   const int fo_toeSafetyReset = 63;// return toe safety limits to default values defined at compile time
```
and I'll have to rewrite the scripts again. might be easier to implement alpha symbols for operation codes.

Closed 2022-02-20.

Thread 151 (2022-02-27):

Add demo MQTTfx script

theAgingApprentice, 2022-02-27:
Remove atest-global script and add hb-example script instead.

theAgingApprentice, 2022-04-11:
Doug has created a script that tests all the legs. There is a separate repo under our Aging Apprentice account that is tracking the creation of a compiler for flows. This ticket can be closed.

Closed 2022-04-11.

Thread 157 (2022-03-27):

Design servo motor controller power management circuit

theAgingApprentice, 2022-03-27:
Design a circuit that will allow the ESP32 MCU to control the power up sequence of the servo motor controller. The steps in the power-up sequence will (roughly) 1. ESP32 does boot up process, 2. Provide 3.3VDC to the PCA9685 processor on the controller board, and 3. Provide power to the 5DVC to the servo motors. The method of providing power to the servo motors must be able to handle 10AMP peak power and normal amps of around 3 AMPs.

nerdoug, 2022-03-28:
[Power-control.odg](https://github.com/va3wam/hexBot/files/8358860/Power-control.odg)

Attached a diagram I did a while ago to illustrate one approach to power management. It's also in the
hexBot/docs/circuitry folder.

nerdoug, 2022-03-28:
need to include pull-up an pull-down resistors to ensure that any signal that's floating because it hasn't been set up yet is pulled in the right direction.

theAgingApprentice, 2022-04-03:
Please add control for 3.3VDC from the ESP32 to the PCA9685 servo controller so that we can control the order that the servo controller CPU starts up and the motor power engages.

nerdoug, 2022-04-09:
I have somewhere between 3 and 6 LH1085 chips, which are 6 pin DIP solid state relays  that can control 3.3 VDC to PCA9685's nicely. have updated the diagram in the docs/circuitry/Power-control.odg file.

theAgingApprentice, 2022-04-10:
For 5VDC this may be an option: I have been thinking about the power control for our servo motor controllers I think we can very easily control the 3.3 and 5.0 VDC voltages for the PCA96856 servo drivers using a couple of Logic Level Enhancement-Type N-Channel MOSFET transistors.

What I think that we need
1. A MOSFET with a Vgs of 3 VDC (or less) so that the ESP32 can turn it on and off.
2. We are only using this as an on/off switch, not PWM, so the rise and fall time characteristics are not that important to us.
3. We want a transistor that is comfortable working at a constant current of say 3 AMPS
4. We think that peak current could be 18 AMPs

Type of MOSFET
Check out this article: https://circuitjournal.com/which-mosfet-should-you-use-with-arduino
We can pull the pin low to a comma ground to ensure no floating problems and that the gate is closed at boot up.

Which MOSFET
According to this article: https://www.instructables.com/ESP32-and-DC-Motors-Tutorial-Part-1/, theRFP30N06LE MOSFET (spec sheet: https://www.sparkfun.com/datasheets/Components/General/RFP30N06LE.pdf) can be driven by an ESP32.

Where to buy
A pack of 5 of these can be purchased on Amazon Canada for $11.00 ([https://www.amazon.ca/Gikfun-RFP30N06LE-N-Channel-Mosfet-Arduino/dp/B01GNORMWA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](https://www.amazon.ca/Gikfun-RFP30N06LE-N-Channel-Mosfet-Arduino/dp/B01GNORMWA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,aps,175&sr=8-1-spons&psc=1&spLa=ZW5jcnlwdGVkUXVhbGlmaWVyPUEyVERDWkY4MEVIRkJQJmVuY3J5cHRlZElkPUEwNTUxNDkzMzVEUlFWSUdIWlowTyZlbmNyeXB0ZWRBZElkPUEwNDQ5MzE1M1VFRjFWSDBXMUNVNCZ3aWRnZXROYW1lPXNwX2F0ZiZhY3Rpb249Y2xpY2tSZWRpcmVjdCZkb05vdExvZ0NsaWNrPXRydWU=))

If you are up for it check my thinking and let me know if you feel that these are worth purchasing.

theAgingApprentice, 2022-04-11:
I ordered the MOSFETs as well as some extra PCA96856 boards so that we can prototype this circuit.

theAgingApprentice, 2022-04-17:
Another requirement here is to isolate back EMF from the motors so it doe snot interfere with the ICs.

theAgingApprentice, 2022-04-17:
Note that Doug's diagram in the docs/circuitry needs to be updated further but it is the ongoing requirement ref doc and design for this ticket.

nerdoug, 2022-05-23:
Created an initial rough draft of GPIO pin assignments for the functions we can foresee at this point. The actual GPIO choices are likely to change in the board layout process to simplify connections, but this does show that we have enough GPIO pins available, considering their various restrictions, to achieve the current plan, we a few leftover pins.

Notes:
-this assignment considers restrictions on some digit pins that can only be input
- whether the pin coms up with weak pull-up, weak pull-down, or neither was NOT considered
- we avoided using A/D controller 2 because it conflicts with WiFi in some way

Assignment file location is  ..docs/circuitry/GPIO-pins.ods

nerdoug, 2022-05-29:
reference for microprocessor interfacing: https://w9xt.com/page_microdesign_toc.html

nerdoug, 2022-05-30:
updated docs/circuitry/Power-control-2.odg, and GPIO-pins.ods to reflect:
-monitoring 5V voltage at only one point, rather than for each PWM controller
-having both a digital enable signal, and an analog sense signal for the common 5V voltage monitor
-moved 5V current sensors to show how they need to be in series with measured circuit
-used different lines for digital and analog GPIO connections
-added a table listing possible chips for various functions
-added 5V and 3.3V LEDs
-rearranged GPIO pin usage a bit, but ended up using the exact same number of pins in total

nerdoug, 2022-06-17:
current power design is reflected in these block diagrams in ..docs/circuitry/ :

Power-control-VN7050ASTR.odg (reflects use of 7050 to control 25V voltage measurement circuit)
power-test-config.odg (includes voltage divider resistor values for measurement circuits)
voltage-dividers.odg (includes the math used to derive resistor values)

nerdoug, 2022-09-25:
Updated power-test-config.odg to reflect GPIO control better.

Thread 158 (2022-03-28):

Confirm that our robots are wired the same way

theAgingApprentice, 2022-03-28:
Recent testing showed a difference in behaviour between Doug and Andrew's robot. Create a script that moves each leg one at a time and compare the two robots to see if they behave the same. Note that this issue coincided with a voltage regulator failing in Andrew's robot. We expect the script and test to prove that wiring is not the issue.

nerdoug, 2022-03-31:
compiler issues 14 and 15 include a script called testAllLegs.txt / 01__hb-testAllLegs.js  which moves each servo for each leg in succession.

theAgingApprentice, 2022-04-10:
Script shows we are wired the same way but there are issues with motor behaviour. Other tickets track the new issue and this ticket can be closed.

Closed 2022-04-10.

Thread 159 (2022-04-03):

Andrew's robot motors

theAgingApprentice, 2022-04-03:
After using Doug's 01__hb-testAlLegs.js script it appears as if the Hip servo motors for Legs 2,  3 and 6 on Andrew's robot are not working properly.

theAgingApprentice, 2022-04-10:
Using the new command to control each motor individually I see no issues. It appears that the problem is not the motors themselves but either the electrical or code used to run the flows. Doug is doing more testing.

theAgingApprentice, 2022-04-17:
Doug has figured out that the script we originally used does not reveal the issue but with a modified script issues can be highlighted. This suggests that the motors may not be at fault so much as the way in which our code works. We have a few issues that we think are contributing to motor instability.
1) The controllers can come up in funny states. We need better power control of the 3.3 and 5 VDC power to the controllers to address this.
2) While we did increase the capacitors on the controller boards from 450 uF to 1000 uF this still may not be enough. We suspect brown-outs during power up may contribute to the issues of motors starting up in a bad state of either being stiff or limp.
3) We have notice that the quality of the MG996R servo motors is not very good and there is noticeable differences between batches of motors hinting at an inconstant manufacturing process. We are going to switch to HiTec HS-485HB motors to see if that gets rid of some of the issues with "play" that we are seeing.

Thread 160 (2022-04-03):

Doug's servo motors are unhealthy

theAgingApprentice, 2022-04-03:
A complete survey of all 18 motors required with a strong suspicion that replacements are required. Also check out the motor controllers themselves.

nerdoug, 2022-04-11:
my leg 6 definitely has problems. makes a grating sound when you move servo manually, and occasionally jumps unpredictably when moving under program control.

The test all legs scripts doesn't do a very good job of testing. all legs seem to perform OK when it's run, including leg 6. I added coded to dump servo commands and timing, and it all looks right. I'll put it in another disposable issue to keep this one open.

Will write and compile a test leg 5 script, so I can compare a possibly good leg with a known bad one.

nerdoug, 2022-04-11:
added the debug code via issue 164, and followed the full procedure in issue 141, which worked exactly as documented

theAgingApprentice, 2022-04-17:
In addition to the problems documented above here are some other relevant notes. This is the same stuff added to the ticket tracking issues with motors on Andrew's robot. Doug has figured out that the script we originally used does not reveal the issue but with a modified script issues can be highlighted. This suggests that the motors may not be at fault so much as the way in which our code works. We have a few issues that we think are contributing to motor instability.

1) The controllers can come up in funny states. We need better power control of the 3.3 and 5 VDC power to the controllers to address this.
2) While we did increase the capacitors on the controller boards from 450 uF to 1000 uF this still may not be enough. We suspect brown-outs during power up may contribute to the issues of motors starting up in a bad state of either being stiff or limp.
3) We have notice that the quality of the MG996R servo motors is not very good and there is noticeable differences between batches of motors hinting at an inconstant manufacturing process. We are going to switch to HiTec HS-485HB motors to see if that gets rid of some of the issues with "play" that we are seeing.

nerdoug, 2022-09-25:
As we change over to the new motors on a new chassis, the priority of this issue diminishes, or at least is reassessed with the new motors. If the issue is solely with old motors that are no longer used, it's probably not worth investigating.

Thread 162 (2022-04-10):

Calibrate HS-485HB servos & add software adjustment

nerdoug, 2022-04-10:
We can't assume that the new HS-485HB servo motors act exactly the same as the old MG 996R servos. We will likely need to use different PWM numbers for a given rotation, and need to measure the new motors to see how we generate these. Hopefully, the new motors are as consistent as the old ones, and we can use a universal algorithm, with per servo calibration values. This will allow us to fine tune the positioning using a 24 position horn.

nerdoug, 2022-04-10:
new MQTT commands to allow testing of servos:

Servo_Test_PWM  <side (0-1)> <port(0-15)> <PWM (100-500?)>
Shortform: STP
Example: STP 0, 15, 300

Servo_Test_Angle <side (0-1)> <port(0-15)> <angle (-90-+90)>

The second command assumes that you have logic in place to translate angles to PWM, which won't be known right away.

nerdoug, 2022-04-11:
Will need to find some of the new bolts needed to attach new servo horns to leg parts. They're tiny. I found 4 in the right thread in my junk box, but none are long enough to do the job.

theAgingApprentice, 2022-04-11:
Purchased bolts on Amazon. Delivery should be in a couple of days.

nerdoug, 2022-05-12:
software adjustment of servo position was implemented and documented under issue #173, Add robot specific boot up logic. Can't close this issue until testing is done with new servos using new body parts that match mounting bolt positions.

Closed 2022-05-12.

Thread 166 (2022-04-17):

Create a new  robot chassis

theAgingApprentice, 2022-04-17:
As we switch from MG996R to HS-485HB hobby servo motors we will be making 2 main changes.

The first change is that we will move the location of the toe in the neutral position from outside of the knee too directly below the knee. Testing has shown that this will put less stress on the servo motors.

The second change is that we are moving from an M3 metric screw standard to an imperial 2-56 screw standard. This means that our tapped holes now go from 3mm to 0.086 inches. We will be using 2 sizes of drills to accommodate this new screw standard.

1) When we want our 2-56 screws to pass through the part via non threaded holes we will use a 3/32" (0.09375") drill holes. An example of when we do this is the connection of the ankle servo horn to the lower shin.
2) When we want our 2-56 screws to thread into a part we will use a 0.07" drill to make the hole. An example of when we do this is the connection of the foot to the ankle servo.

theAgingApprentice, 2022-04-18:
Have a new foot design and have saved the tool paths as a template in the cloud. Feeds are OK and finish seems passable.
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

nerdoug, 2022-04-18:
looks good. The foot looks shorter than the old one, or it this just my pathetic eyesight? Wondering if having the stub at the end a little longer would make it easier to attach "boots" is a stable way?

nerdoug, 2022-04-18:
Having the foot length variable depending on whether or not a boot is attached, and how thick it is, would complicate the math. Maybe we should adopt a standard boot thickness, and either never have him go barefoot, or accept inaccuracies if he does.

theAgingApprentice, 2022-04-19:
I think it must be the perspective of the model I choose to show the new design. The new foot is exactly the same length as the old one. This may be an issue now that I think of it. My plan is to machine shoes that will add to the foot length. I guess I can shorten the leg to account for the shoe. My plan is to porches rubber coating that we can dip the shoes into to get grippy feet.

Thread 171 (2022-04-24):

Update diagrams in high level design document. Also rename document.

theAgingApprentice, 2022-04-24:
The diagrams for the servo motor and the foot do not include the size of the holes being drilled. It also does not show the thickness of the material or the units that measurement are expressed in. A seperate diagram for the shoe is needed. Finally, the dcument is currently called hexaFlooRideHighLevelDesign.odt. Renaming it to hexaFloorRideHighLevelDesign.odt as because it is easier to understand how to pronounce it at a glance when written this way.

Closed 2022-04-25.

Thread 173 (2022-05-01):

Add robot specific boot up logic

theAgingApprentice, 2022-05-01:
Make a dummy routine called setConfig() in the configDetails.cpp include file that executes at startup and gives as a place to set global variables based on Mac address.

nerdoug, 2022-05-12:
There's now a routine called setupPerBotConfig() in flows.cpp. It's called from setup() in main. The only thing it does so far is set the software defined PWM values for each servo's center position to 299.

This was actually implemented under issue 162

In retrospect, I see that I didn't follow the plan of creating a routine called setConfig() in the configDetails.cpp include file. I can move the code there if that would be better.

Closed 2022-05-12.

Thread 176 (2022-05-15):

issue warning if mapDegToPWM()  modifies requested angle

nerdoug, 2022-05-15:
mapDegToPWM translates a desired servo angle to the PWM value needed to achieve that. It does a safety check to ensure that the requested angle is between -90 and +90 degrees. If the value is outside this range, it is modified to be the closest part of the range, (which could still be dangerous if it causes a collision with a body part or another leg).

This routine will now issue a console message if it modifies a requested angle as a result of this check. Will also change the value 90 from  a hard coded "90" to the symbol maxServoAngle so this range can be easily restricted further.

nerdoug, 2022-05-15:
Also moved setupPerBotConfig() from flows.cpp to configDetails.cpp

Closed 2022-05-15.

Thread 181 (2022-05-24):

update Power control diagram

nerdoug, 2022-05-24:
Need to include separate sensing and control of 5V power for each PCA9685 board, and separate control for 3.3 V.

nerdoug, 2022-05-24:
updated power design document Power-control-2.odg added to ..docs/circuitry.

Closed 2022-05-24.

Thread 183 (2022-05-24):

corrections to doc/circuitry/GPIO-pins.ods

nerdoug, 2022-05-24:
Found some confusion between physical and GPIO pin numbering, and some further restrictions:
- we can use physical pin 24 / GPIO 12 because it prevents software downloading from working
- physical 25, GPIO 13 is connected to CPU's onboard LED, so we should probably avoid it

Looked up "input only" and "output only" status of various pins, and made corrections in column O, which was copied from a source file.

Added references for Adafruit site (which determines what Huzzah physical pins are connected to what CPU pins/ GPIO functions)
and 2 Espressif sites (for definition of GPIO behaviour) in top right corner of page.

At the moment the pin assignments include:
- two I2C buses
- no 3.3 V sensing of voltage or current, just on/off control
- only one OLED board button
- no connections to physical pins 24 & 25 as discussed above

With these restrictions, there are 19 GPIO pins available, and we're using them all, with no spares (unless we don't need the second I2C bus).

Closed 2022-05-24.

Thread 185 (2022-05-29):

fix the power control diagram

nerdoug, 2022-05-29:
minor line drawing error

nerdoug, 2022-05-30:
will be fixed as part of issue 187: adjust power design for 2 pins for 5V power sensing

Closed 2022-05-30.

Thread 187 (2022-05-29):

adjust  power design for 2 pins for 5V Voltage sensing

nerdoug, 2022-05-29:
To read the 5 Volt signal, we need a GPIO pin that enables the measurement circuitry (MOSFET) and A/D pin to read the input signal from the voltage divider. Need to change GPIO assignments, and update power control diagram.

As part of this we've committed to using a single measurement of 5V power.

Could also explore I2C devices that measure voltage to save GPIO pins.

nerdoug, 2022-05-30:
Also made adjustments to GPIO-pins.ods to reflect changes needed for going to a single voltage monitor point for 5 Volts.

Closed 2022-05-30.

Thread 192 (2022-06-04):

create power control scheme using VN7050ASTR MOSFET

nerdoug, 2022-06-04:
In pursuing how to implement high side switching for 5V power control, I came across the STM VN7050ASTR chip which has a lot going for it:

On Thu, Jun 2, 2022 at 6:51 PM Doug Elliott <[canoe.eh@gmail.com](mailto:canoe.eh@gmail.com)> wrote:
This seems too good to be true:
  https://www.mouser.ca/ProductDetail/STMicroelectronics/VN7050ASTR?qs=N2Tevpb%252BvoaSglANpOhF3A%3D%3D

- high side switch
- up to 40 V
- up to 30 A
- control signals compatible with 3 and 5 Volt systems ( no level converters or Darlington's needed)
- built in current measurement
- 8 pin SO-9 package - surface mount, for 1 switched channel
- (need to verify that current sensing works on 8 pin part that's missing some SEL pins)
- in stock at Mouser
- $2.68 CDN each

I've since verified that the 8 pin part does support current sensing. They did reduce the functionality on the 8 pin part, but they maintained the ability to measure current:

Reference: ST Microelectronics  Application note UM1922 (attached)
- section 5
- table 15
- page 59
[um1922-vipower-m07-standard-highside-drivers-hardware-design-guide-stmicroelectronics.pdf](https://github.com/va3wam/hexBot/files/8836645/um1922-vipower-m07-standard-highside-drivers-hardware-design-guide-stmicroelectronics.pdf)

We still need to drive SELn High to get the current measurement feedback, but we could strap it rather than use a GPIO.

We could use this chip for all of our software controlled circuits:
- 5V enable, for both PCA9685's
- 3.3V enable, for both PCA9685's
- enable/disable the Battery Voltage measuring circuit
- enable/disable the 5V voltage measuring system.

The purpose of this issue is to create a power diagram version that uses the VN7050ASTR for all of these functions, for discussion purposes.

nerdoug, 2022-06-04:
Snag: The circuit that the VN7050ASTR controls is specified as having a voltage above 4 volts, which means we can't use it to control the 3.3V circuit to the PCA9685's.  There's probably another chip variation we can use. Some possibilities:
    STMPS2242, 2252, 2262, 2272
    STMPS2141....

nerdoug, 2022-06-10:
I have ordered and received a bunch of VN7050ASTR chips for 5V enable/disable, and current reading.
I also got a bunch of STMPS2141AMTTR chips to control the 3.3 V feed to the PCA9685's and to enable/disable the voltage divider used to measure battery voltage.

I done some breadboard testing, and they operate as expected with one exception: The sense of the EN pin on the 2141 is opposite to the 7050. On the 2141, if you put a logic high on the EN pin, it OPENS the switch. On the 7050, a logic high on INPUT CLOSES the switch. I don't think this is a problem, and we just need to adjust software, pullup/down resistors, and possibly the choice of GPIOs.

This behaviour doesn't seem to be mentioned in the 2141 data sheet, but it's implied in the diagrams in sections 7.1.1 and 7.1.2.

I've also made up a cheat sheet that shows how the chip pins are connected to the DIP carrier's pins, with a description of the pin function.  ..doc/circuitry/soic-8-adapters-pinouts.odg and pdf.

nerdoug, 2022-06-10:
I also put datasheets for the 7050 and 2141 into /docs/circuitry/datasheets

Closed 2022-06-10.

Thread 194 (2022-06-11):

adjust power control circuit

nerdoug, 2022-06-11:
The 2141 chip used as enable for the voltage divider didn't need to handle much voltage when it was on the low side, connected to ground. When I moved it to the high  side, on 25V, I exceeded the chip's voltage capacity of 2.7 - 5.5V. There are 2 possible solutions:
1) Use 7050 chips which can handle 25V instead
2) Put in a resistor to bring the voltage down before it gets to the 2141.

I'm putting in the resistor to make best use of the chips we already have, and will breadboard the circuit to test it.

Result will be a new version of ..docs/circuitry/Power-control-VN7050ASTR.odg

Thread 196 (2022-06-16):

figure out 5V current measuring voltage divider

nerdoug, 2022-06-16:
Need to understand how current measurement works on the 7050 chip, calculate the resistor values for the voltage dividers, and update:
1) voltage-dividers.odg
2) power-test-config.odg

The voltage-dividers.odg file has the framework for the calculations on the right side, just need to determine some input values.

nerdoug, 2022-06-22:
We saw an indication that the MultiSense signal that provides current measurement does this by providing a varying current on the MS pin. This came as a surprise, and I'm trying to find that reference again.

The User manual document for the VIPower series of chips, that includes the 7050, has diagrams that show MS pin connected to a microprocessor A/D pin, which implies that the current measurement is represented by a voltage.
Reference: UM1693 document (which I'll put in the datasheets folder), section 5.3, figure 37. This shows 3 power control devices, each with a multisense output that has this path:
- a tap to a pull-down resistor Rsense just outside the chip
- a 15K resistor in series with the path
- a tap to a 470 pF capacitor to ground
- a connection to a microprocessor pin with a label like A/D 1

Note also the 100nF decoupling capacitors on the power control chips. Attempting to attach a copy of figure 37.
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

nerdoug, 2022-06-22:
UM1693 provides further info on Multisense (MS) in section 7, section 7.2.1 in particular. It seems that the MS pin delivers a current that is proportional to the load current. However, the external Rsense resistor converts this to a voltage level. It's not clear how you select the value for the Rsense resistor, but if we're lucky, we can select it to create an output voltage that's compatible with the ESP32 A/D hardware, and avoid another voltage divider.

Rsense calculation is covered in section 7.2.5, and 7.2.6 . Needs further investigation, as it's a bit complicated.

nerdoug, 2022-07-03:
see docs/current-sensing.odg for musings on Rsense controlling a current divider

nerdoug, 2022-07-03:
The current measuring circuit seems to be a current divider, as explained in:
   https://www.electronics-tutorials.ws/dccircuits/current-divider.html
   https://blog.ttelectronics.com/current-sense-resistors

nerdoug, 2022-09-25:
Need to breadboard the power control circuitry, and write some software to exercise the functionality, as a proof of concept.

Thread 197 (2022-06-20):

fix resistor typo in power-test-config.odg

nerdoug, 2022-06-20:
25V divider should have a 30 Ohm resistor, not 300.

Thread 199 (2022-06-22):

Add 7050 chip user manual to datasheets folder

nerdoug, 2022-06-22:
The 7050 is part of a family of chips called VIPower by its manufacturer STM. There is a user manual for the family that includes a lot of useful information on how to use an configure the chips. I've put it into the datasheets folder as UM1693.pdf

nerdoug, 2022-06-22:
Also updated power-test-config.odg, and voltage-dividers.odg to reflect changes in 5V current measurement technique.

Closed 2022-06-22.

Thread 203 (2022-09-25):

fixes to power-test-config.odg

nerdoug, 2022-09-25:
clarify how the controlling GPIO signals connect to the circuit

nerdoug, 2022-09-25:
...so I can upload the file.

Closed 2022-09-25.

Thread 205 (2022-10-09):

create Eagle component for 7050 & 2141 chips on DIP headers

nerdoug, 2022-10-09:
We'll breadboard the power control circuitry using the 7050 and 2141 chips mounted on DIP headers so they're physically compatible with breadboards. In order to properly document the actual circuit we need to have corresponding components defined in Eagle.

For the production circuit boards, we could either use the DIP mounted components in sockets, or put the surface mount chips right on the PCB.  It's probably possible to replace an SMD chip, but we might need a special rework station with a specialized hot air gun. (which would be a good thing to have anyway.)

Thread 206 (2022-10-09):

Document why we selected the 7050 and 2141 ICs

theAgingApprentice, 2022-10-09:
Using issue 145, 157 and 196 update our documentation to explain
1. Why we chose the 2141 and 7050 ICs for power management and monitoring
2. Why we measure current in multiple places but voltage in only 1 location
3. The chart that shows how 25V, 5V and 3.3V are managed (on whiteboard)

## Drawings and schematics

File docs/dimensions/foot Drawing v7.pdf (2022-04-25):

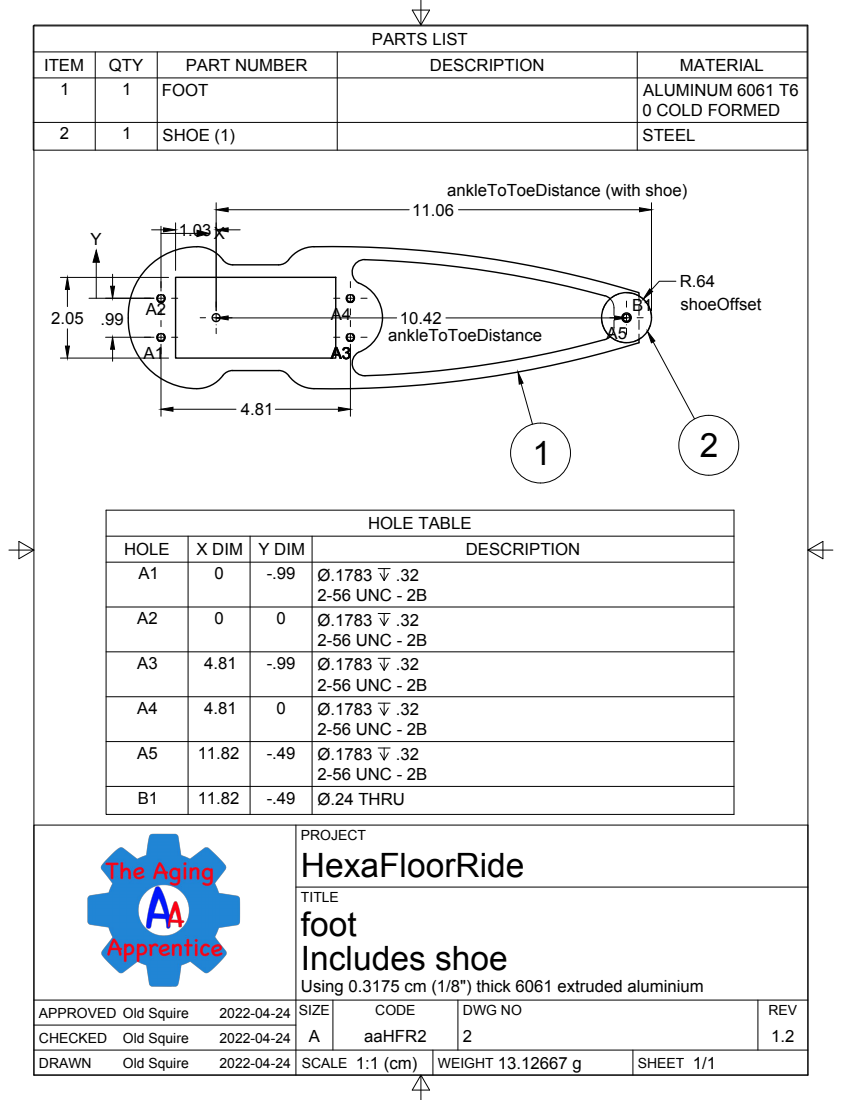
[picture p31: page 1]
SIZE; CODE; DWG NO; REV; Old Squire; aaHFR2; Includes shoe; PARTS LIST; HOLE TABLE

ITEM | QTY | PART NUMBER | DESCRIPTION | MATERIAL
1 | 1 | FOOT | | ALUMINUM 6061 T6 0 COLD FORMED

2 | 1 | SHOE (1) | | STEEL

ankleToToeDistance (with shoe)

HOLE | X DIM | Y DIM | DESCRIPTION
A1 | 0 | -.99 | Ø.1783 .32 2-56 UNC - 2B

A2 | 0 | 0 | Ø.1783 .32 2-56 UNC - 2B

A3 | 4.81 | -.99 | Ø.1783 .32 2-56 UNC - 2B

A4 | 4.81 | 0 | Ø.1783 .32 2-56 UNC - 2B

A5 | 11.82 | -.49 | Ø.1783 .32 2-56 UNC - 2B

B1 | 11.82 | -.49 | Ø.24 THRU

Using 0.3175 cm (1/8") thick 6061 extruded aluminium

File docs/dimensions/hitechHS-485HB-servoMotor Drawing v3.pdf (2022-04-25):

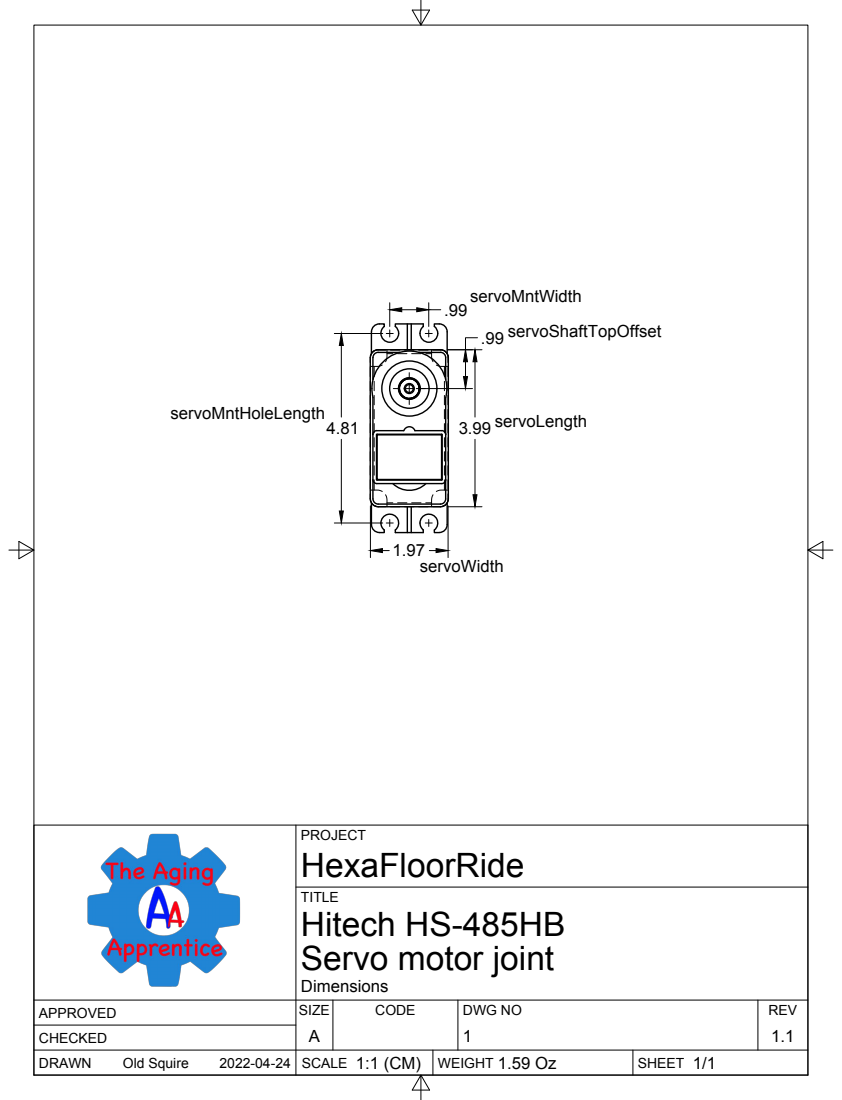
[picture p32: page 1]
SIZE; CODE; DWG NO; REV; Old Squire

PROJECT
HexaFloorRide
Hitech HS-485HB
Servo motor joint

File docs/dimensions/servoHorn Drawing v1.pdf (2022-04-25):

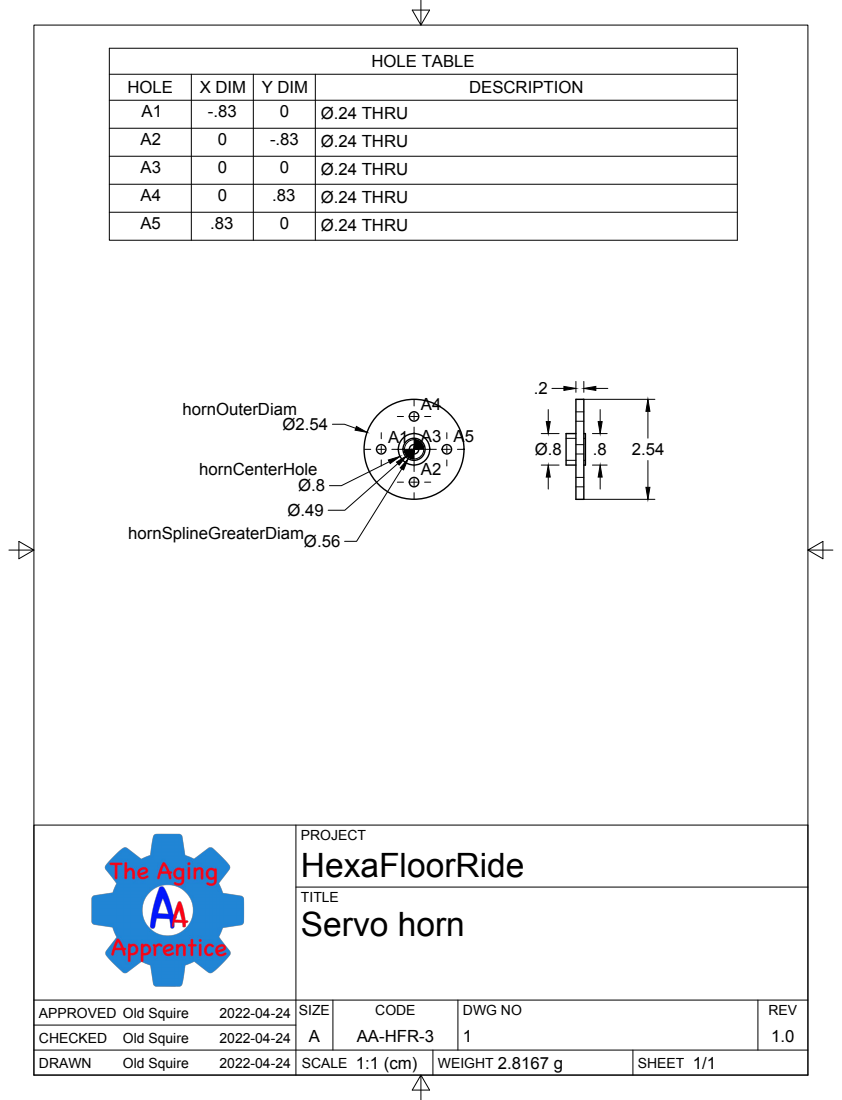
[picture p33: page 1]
SIZE; CODE; DWG NO; REV; Old Squire; AA-HFR-3; Servo horn; HOLE TABLE

HOLE | X DIM | Y DIM | DESCRIPTION
A1 | -.83 | 0 | Ø.24 THRU
A2 | 0 | -.83 | Ø.24 THRU
A3 | 0 | 0 | Ø.24 THRU
A4 | 0 | .83 | Ø.24 THRU
A5 | .83 | 0 | Ø.24 THRU

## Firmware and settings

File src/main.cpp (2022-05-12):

/******************************************************************************
 * @file main.cpp
 *
 * @mainpage Hexbot firmware. 
 * 
 * @section intro_sec Introduction
 *
 * This code is the firmware for the six legged robot called Hexbot. Full
 * details on how to get the circuit and chassis for this robot are found
 * [here](https://github.com/va3wam/hexBot). 
 *
 * @section dependencies Dependencies
 * 
 * This sketch depends on the libraries located in the main.h file located in
 * the include directory of this repository.
 *
 * @section author Author(s)
 *
 * Written by Old Squire and Doug Elliott.
 *
 * @section license license
 *
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
 * THE SOFTWARE IS PROVIDED "AS IS", WITHOUT WARRANTY OF ANY KIND, EXPRESS OR 
 * IMPLIED, INCLUDING BUT NOT LIMITED TO THE WARRANTIES OF MERCHANTABILITY, 
 * FITNESS FOR A PARTICULAR PURPOSE AND NONINFRINGEMENT. IN NO EVENT SHALL THE
 * AUTHORS OR COPYRIGHT HOLDERS BE LIABLE FOR ANY CLAIM, DAMAGES OR OTHER 
 * LIABILITY, WHETHER IN AN ACTION OF CONTRACT, TORT OR OTHERWISE, ARISING 
 * FROM, OUT OF OR IN CONNECTION WITH THE SOFTWARE OR THE USE OR OTHER DEALINGS
 * IN THE SOFTWARE.  
 *****************************************************************************/
#include <main.h> // Header file for all libraries needed by this program.
unsigned long timer; // Milli count for next action.

/**
 * @brief Standard Arduino initialization routine.
 * ==========================================================================*/
void setup() 
{
   setupSerial(); // Set serial baud rate. 
   Log.begin(LOG_LEVEL_VERBOSE, &Serial, true);
   Log.traceln("<setup> Start of setup."); 
   Log.verboseln("<setup> Initialize I2C buses.");  
   Wire.begin(G_I2C_BUS0_SDA, G_I2C_BUS0_SCL, I2C_BUS0_SPEED); // Init I2C bus0.
   scanBus0(); // Scan bus0 and show connected devices.
   Log.traceln("<setup> Initialize OLED.");
   initOled();
   Log.verboseln("<setup> Initialize status RGB LED."); 
   setupStatusLed(); // Configure the status LED on the reset button.
   setStdRgbColour(WHITE); // Indicates that boot up is in progress.
   Log.verboseln("<setup> Set up wifi connection."); 
   setupNetwork();
   setupPerBotConfig();    // do setup unique to each hexbot. 
         //code for above routine is in flows.cpp
   Log.traceln("<setup> Initialize servo drivers.");
   setupMobility();
   Log.verboseln("<setup> Display robot configuration in console trace."); 
   showCfgDetails(); // Show all configuration details in one summary.
   Log.verboseln("<setup> Initialize flows.");
   setupFlows();
   Log.verboseln("<setup> Review status flags to see how boot sequence went."); 
   checkBoot();   
   timer = millis(); // Timer for motor driver signalling.
   Log.traceln("<setup> End of setup."); 
} // setup()

/**
 * @brief Standard Arduino main loop.
 * ==========================================================================*/
void loop() 
{
// check for hi priority 20msec loop first. Should serialize other tasks too,
//  so at most one of them is done per loop()
// ==== track how well we're doing at running the 20msec on time.   
   if(f_flowing == true)  // are we executing a predefined flow between positions?
   {   do_flow();           // yes. caclulate and do next servo commands. It's in flow.cpp module
   }  
   monitorWebServer(); // Handle any pending web client requests. 
   checkOledButtons(); // Check if an OLED button has been pressed.
   checkMqtt(); // Check the MQTT message queue for incoming commands.
} // loop()  

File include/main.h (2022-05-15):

/*******************************************************************************
 * @file main.h  
 *******************************************************************************/
#ifndef main_h // Start of precompiler check to avoid dupicate inclusion of this code block.

#define main_h // Precompiler macro used for precompiler check.

/*******************************************************************************
 * @section mainIncludes Included libraries.
 *******************************************************************************/
#include <Arduino.h> // Arduino Core for ESP32. Comes with PlatformIO.
#include <aaChip.h> // Core (CPU) details that the code running on.
#include <aaNetwork.h> // Wifi functions. 
#include <aaWebService.h> // Realtime web-based network config and OTA code updates.
#include <aaFlash.h> // Use Flash memory to store values that persist past reboot.
#include <aaMqtt.h> // Use MQTT for remote management and monitoring.
#include <known_networks.h> // String arrays of known Access Points and their passwords.
#include <InverseK.h> // https://github.com/cgxeiji/CGx-InverseK.
#include <Wire.h> // Required for I2C communication.
#include <Adafruit_PWMServoDriver.h> // https://github.com/adafruit/Adafruit-PWM-Servo-Driver-Library.
#include <ArduinoLog.h> // https://github.com/thijse/Arduino-Log.
#include <Adafruit_GFX.h> // OLED graphics
#include <Adafruit_SH110X.h> // OLED text
#include <hexbot_gpio_pins.h> // GPIO pin uses
#include <flows.h>      // parameter definitions and global storage for flows that define leg movement

/*******************************************************************************
 * @section mainVars Global variable definitions.
 * @details In order to get rid of "error: 'xxx' was not declared in this scope"
 * compiler errors list a function from any of the include files here. 
 *******************************************************************************/
// Config related variables
const char* HOST_NAME_PREFIX = "Hexbot"; // Prefix for our unique network name.
aaChip appCpu; // Access information about the ESP32 application microprocessor (Core1).
aaNetwork network(HOST_NAME_PREFIX); // WiFi session management.
bool networkConnected = false;
bool mqttBrokerConnected = false;
bool oledConnected = false;
bool motorController1Connected = false;
bool motorController2Connected = false;
bool mobilityStatus = false;
int8_t displayPage = 1;
// MQTT related variables.
aaFlash flash; // Non-volatile memory management. 
aaMqtt mqtt; // Publish and subscribe to MQTT broker. 
IPAddress brokerIP; // IP address of the MQTT broker.
char uniqueName[HOST_NAME_SIZE]; // Character array that holds unique name for Wifi network purposes. 
char *uniqueNamePtr = &uniqueName[0]; // Pointer to first address position of unique name character array.
char healthTopicTree[50] = ""; // Char array to hold full health topic tree name.
char helpTopicTree[50] = ""; // Char array to hold full health topic tree name.
String result[2] = {"false","true"}; // Provide english lables for true and flase return codes.
// RGB OLED related variabes.
const uint8_t numColoursSupported = 9; // Number of colours LED can be set to.
const bool commonAnode = true; // Set to true if RGB LED has a common anode, false for common cathode.
const uint8_t RED = 0; // Reset button LED red. 
const uint8_t GREEN = 1; // Reset button LED green. 
const uint8_t BLUE = 2; // Reset button LED blue. 
const uint8_t YELLOW = 3; // Reset button LED YELLOW. 
const uint8_t ORANGE = 4; // Reset button LED PINK.
const uint8_t PINK = 5; // Reset button LED PINK.
const uint8_t AQUA = 6; // Reset button LED aqua. 
const uint8_t WHITE = 7; // Reset button LED white. 
const uint8_t BLACK = 8; // Reset button LED white. 
const double_t PWM_FREQ = 500; // 500Hz.
const uint8_t PWM_RESOLUTION = 8; // ESP32 can go up to 8 bit PWM resolution.
#define PWM_RED_CHANNEL 0 // ESP32 has 16 channels which can generate 16 independent waveforms. Use 0 for RGB red.
#define PWM_GREEN_CHANNEL 1 // ESP32 has 16 channels which can generate 16 independent waveforms. Use 1 for RGB green.
#define PWM_BLUE_CHANNEL 2 // ESP32 has 16 channels which can generate 16 independent waveforms. Use 2 for RGB blue.
typedef struct
{
   String name; // Name associated with colour properties
   uint32_t redDutyCycle; // Up time of the PWM signal. Ranges from 0-256. 127 is a 50% duty cycle for example.
   uint32_t greenDutyCycle; // Up time of the PWM signal. Ranges from 0-256. 127 is a 50% duty cycle for example.
   uint32_t blueDutyCycle; // Up time of the PWM signal. Ranges from 0-256. 127 is a 50% duty cycle for example.
}struct_Colour; 
struct_Colour statusColour[numColoursSupported]; // Array of colours.
struct_Colour memColour; // Used to switch back RGB LED colour when it is temporarily changed.
// DAE Inverted kinematic related variables.
const float footLen = 11; // Distance from ankle to toe (foot) is 11cm.
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

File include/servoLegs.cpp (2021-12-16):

/*******************************************************************************
 * @file servoLegs.cpp  
 * @brief File containing all reset button RGB LED functions.
 *******************************************************************************/
#ifndef servoLegs_cpp // Start of precompiler check to avoid dupicate inclusion of this code block.

#define servoLegs_cpp // Precompiler macro used for precompiler check.

#include <main.h> // Header file for all libraries needed by this program.

/**
 * @brief Put leg in neutral position.
 * 
 * @details Each leg is connected to a PWM pin on a servo motor driver. There 
 * are 2 motor drivers on hexbot. One driver handles all the motors used for 
 * the legs on the left side. Another motor driver handles all of the motors 
 * used for the right side. Each leg is made up of three joints. 
 * 
 * @param driver One of the 16 channel motor drivers (0-1).
 * @param leg One of the three legs on one side of the robot (0-2).
 * ==========================================================================*/
void startPositionLegs(int8_t driverNum, int8_t legNum) 
{
   Log.noticeln("<startPositionLeftLegs> Put %s leg into starting position.", leg[driverNum][legNum].description.c_str());
   Log.noticeln("<startPositionLeftLegs> ...Move knee.");
   pwmDriver[driverNum].setPWM(leg[driverNum][legNum].kneePinNum, pwmClkStart, leg[driverNum][legNum].maxUp);
   delay(100);
   Log.noticeln("<startPositionLeftLegs> ...Move hip.");
   pwmDriver[driverNum].setPWM(leg[driverNum][legNum].hipPinNum, pwmClkStart, servoMiddlePWM);
   delay(100);
   Log.noticeln("<startPositionLeftLegs> ...Move toe.");
   pwmDriver[driverNum].setPWM(leg[driverNum][legNum].anklePinNum, pwmClkStart, servoMiddlePWM);
   delay(100);
   legDirIndex = 0; // Indicate that legs are currently in home position.
} // startRightLeg()

/**
 * @brief Initialize serv motor control.
 * ==========================================================================*/
// TODO #29 leg array description field in function initServos() corrupted.
void initServos() 
{
   int8_t driver; // Left or right driver number
   int8_t legNum; // Front, middle or back leg on specific side

   Log.traceln("<initServo> Set up Explanation for each motor directive.");
   legDirExpl[HOME_POSITION] = "home position";
   legDirExpl[STAND_POSITION] = "stand position";
   legDirExpl[CROUCH_POSITION] = "crouch position";
   legDirExpl[LEAN_LEFT] = "lean left";
   legDirExpl[LEAN_RIGHT] = "lean right";
   legDirExpl[LEAN_FORWARD] = "lean forward";
   legDirExpl[LEAN_BACKWARD] = "lean backward";
   Log.traceln("<initServo> Set up motor definitions for each leg on right driver.");
   driver = 0; // Right servo motor driver
   legNum = 0; // First leg on right side
   leg[driver][legNum].description = "right front";
   Log.noticeln("<initServo> Driver = %d, Motor Num = %d, Desc = %s.", driver, legNum, leg[driver][legNum].description.c_str());
   leg[driver][legNum].driverAdd = PCA9685ServoDriver1;
   Log.noticeln("<initServo> Driver address = %X.", leg[driver][legNum].driverAdd);
   leg[driver][legNum].hipPinNum = 0;
   leg[driver][legNum].kneePinNum = 1;
   leg[driver][legNum].anklePinNum = 2;
   Log.noticeln("<initServo> Hip = %d, knee = %d, toe = %d.", leg[driver][legNum].hipPinNum, leg[driver][legNum].kneePinNum, leg[driver][legNum].anklePinNum);
   leg[driver][legNum].maxUp = servoMiddlePWM - servoUpDownSwing;
   leg[driver][legNum].maxDown = servoMiddlePWM + servoUpDownSwing;
   leg[driver][legNum].maxFront = servoMiddlePWM + servoFrontBackSwing;
   leg[driver][legNum].maxBack = servoMiddlePWM - servoFrontBackSwing;
   legNum ++; // Middle leg on right side
   leg[driver][legNum].description = "right middle";
   Log.noticeln("<initServo> Driver = %d, Motor Num = %d, Desc = %s.", driver, legNum, leg[driver][legNum].description.c_str());
   leg[driver][legNum].driverAdd = PCA9685ServoDriver1;
   Log.noticeln("<initServo> Driver address = %X.", leg[driver][legNum].driverAdd);
   leg[driver][legNum].hipPinNum = 3;
   leg[driver][legNum].kneePinNum = 4;
   leg[driver][legNum].anklePinNum = 5;
   Log.noticeln("<initServo> Hip = %d, knee = %d, toe = %d.", leg[driver][legNum].hipPinNum, leg[driver][legNum].kneePinNum, leg[driver][legNum].anklePinNum);
   leg[driver][legNum].maxUp = servoMiddlePWM - servoUpDownSwing;
   leg[driver][legNum].maxDown = servoMiddlePWM + servoUpDownSwing;
   leg[driver][legNum].maxFront = servoMiddlePWM + servoFrontBackSwing;
   leg[driver][legNum].maxBack = servoMiddlePWM - servoFrontBackSwing;
   legNum ++; // Back leg on right side
   leg[driver][legNum].description = "right back";
   Log.noticeln("<initServo> Driver = %d, Motor Num = %d, Desc = %s.", driver, legNum, leg[driver][legNum].description.c_str());
   leg[driver][legNum].driverAdd = PCA9685ServoDriver1;
   Log.noticeln("<initServo> Driver address = %X.", leg[driver][legNum].driverAdd);
   leg[driver][legNum].hipPinNum = 6;
   leg[driver][legNum].kneePinNum = 7;
   leg[driver][legNum].anklePinNum = 8;
   Log.noticeln("<initServo> Hip = %d, knee = %d, toe = %d.", leg[driver][legNum].hipPinNum, leg[driver][legNum].kneePinNum, leg[driver][legNum].anklePinNum);
   leg[driver][legNum].maxUp = servoMiddlePWM - servoUpDownSwing;
   leg[driver][legNum].maxDown = servoMiddlePWM + servoUpDownSwing;
   leg[driver][legNum].maxFront = servoMiddlePWM + servoFrontBackSwing;
   leg[driver][legNum].maxBack = servoMiddlePWM - servoFrontBackSwing;
   Log.traceln("<initServo> Set up motor definitions for each leg on left driver.");
   driver = 1; // Left servo motor driver
   legNum = 0; // First leg on left side
   leg[driver][legNum].description = "left front";
   leg[driver][legNum].driverAdd = PCA9685ServoDriver2;
   leg[driver][legNum].hipPinNum = 0;
   leg[driver][legNum].kneePinNum = 1;
   leg[driver][legNum].anklePinNum = 2;
   leg[driver][legNum].maxUp = servoMiddlePWM + servoUpDownSwing;
   leg[driver][legNum].maxDown = servoMiddlePWM - servoUpDownSwing;
   leg[driver][legNum].maxFront = servoMiddlePWM + servoFrontBackSwing;
   leg[driver][legNum].maxBack = servoMiddlePWM - servoFrontBackSwing;
   legNum ++; // Middle leg on left side
   leg[driver][legNum].description = "left middle";
   leg[driver][legNum].driverAdd = PCA9685ServoDriver2;
   leg[driver][legNum].hipPinNum = 3;
   leg[driver][legNum].kneePinNum = 4;
   leg[driver][legNum].anklePinNum = 5;
   leg[driver][legNum].maxUp = servoMiddlePWM + servoUpDownSwing;
   leg[driver][legNum].maxDown = servoMiddlePWM - servoUpDownSwing;
   leg[driver][legNum].maxFront = servoMiddlePWM + servoFrontBackSwing;
   leg[driver][legNum].maxBack = servoMiddlePWM - servoFrontBackSwing;
   legNum ++; // Back leg on left side
   leg[driver][legNum].description = "left back";
   leg[driver][legNum].driverAdd = PCA9685ServoDriver2;
   leg[driver][legNum].hipPinNum = 6;
   leg[driver][legNum].kneePinNum = 7;
   leg[driver][legNum].anklePinNum = 8;
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

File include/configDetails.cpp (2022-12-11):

/*******************************************************************************
 * @file configDetails.cpp  
 * @brief setup & display config parameters and boot status
 *******************************************************************************/
#ifndef showCfgDetails_cpp // Start of precompiler check to avoid dupicate inclusion of this code block.

#define showCfgDetails_cpp // Precompiler macro used for precompiler check.

#include <main.h> // Header file for all libraries needed by this program.


/**
 * @brief Do configuration set up that is unique to each robot, including:
 * - define servo calibration offset values
 * called from setup() in main.cpp
 * tried to put this routine in hexBot/lib/aaWeb-1.0.0/lib/aaNetwork-main/src/aaNetwork.cpp
 *    but couldn't get it to work, due to object structure issues I suspect
 =============================================================================*/
 void setupPerBotConfig()     // do the robot-specific setup
 {
    String macAdd = WiFi.macAddress(); // Get MAC address as String
    sp2("<setupPerBotConfig> MAC Address: ", macAdd);  // see if we can read this variable
    if(macAdd == "3C:61:05:4A:DD:98")  // Doug's robot 1 MAC address
    {
       sp1l("  Doing bot-specific setup for Doug's robot 1 MAC address");
       // set up the servo calibration offsets
       // PWM value used = (PWM calculated from angle) + (calibration offset for this servo) - 299
       // note that servoOffset[0] is not used
       servoOffset[ 1] = 299;
       servoOffset[ 2] = 299;
       servoOffset[ 3] = 299;
       servoOffset[ 4] = 299;
       servoOffset[ 5] = 299;
       servoOffset[ 6] = 299;
       servoOffset[ 7] = 299;
       servoOffset[ 8] = 299;
       servoOffset[ 9] = 299;
       servoOffset[10] = 299;
       servoOffset[11] = 299;
       servoOffset[12] = 299;
       servoOffset[13] = 299;
       servoOffset[14] = 299;
       servoOffset[15] = 299;
       servoOffset[16] = 299;
       servoOffset[17] = 299;
       servoOffset[18] = 299;

    }
    else if(macAdd == "94:B9:7E:5F:4A:40")  // Andrew's robot 1 MAC address
    {
       sp1l("  Doing bot-specific setup for Andrew's robot 1 MAC address");
       // set up the servo calibration offsets
       // PWM value used = (PWM calculated from angle) + (calibration offset for this servo)
       // note that servoOffset[0] is not used
       servoOffset[ 1] = 299;
       servoOffset[ 2] = 299;
       servoOffset[ 3] = 299;
       servoOffset[ 4] = 299;
       servoOffset[ 5] = 299;
       servoOffset[ 6] = 299;
       servoOffset[ 7] = 299;
       servoOffset[ 8] = 299;
       servoOffset[ 9] = 299;
       servoOffset[10] = 299;
       servoOffset[11] = 299;
       servoOffset[12] = 299;
       servoOffset[13] = 299;
       servoOffset[14] = 299;
       servoOffset[15] = 299;
       servoOffset[16] = 299;
       servoOffset[17] = 299;
       servoOffset[18] = 299;
    }
    else if(macAdd == "94:B9:7E:5F:48:B8")  // Doug's robot 2 MAC address
    {
       sp1l("  Doing bot-specific setup for Doug's robot 2 MAC address");
       // set up the servo calibration offsets
       // PWM value used = (PWM calculated from angle) + (calibration offset for this servo) - 299
       // note that servoOffset[0] is not used
       servoOffset[ 1] = 299;
       servoOffset[ 2] = 299;
       servoOffset[ 3] = 299;
       servoOffset[ 4] = 299;
       servoOffset[ 5] = 299;
       servoOffset[ 6] = 299;
       servoOffset[ 7] = 299;
       servoOffset[ 8] = 299;
       servoOffset[ 9] = 299;
       servoOffset[10] = 299;
       servoOffset[11] = 299;
       servoOffset[12] = 299;
       servoOffset[13] = 299;
       servoOffset[14] = 299;
       servoOffset[15] = 299;
       servoOffset[16] = 299;
       servoOffset[17] = 299;
       servoOffset[18] = 299;

    }
    else if(macAdd == "94:B9:7E:5F:52:DC")  // Andrew's robot 2 MAC address
    {
       sp1l("  Doing bot-specific setup for Andrew's robot 2 MAC address");
       // set up the servo calibration offsets
       // PWM value used = (PWM calculated from angle) + (calibration offset for this servo)
       // note that servoOffset[0] is not used
       servoOffset[ 1] = 299;
       servoOffset[ 2] = 299;
       servoOffset[ 3] = 299;
       servoOffset[ 4] = 299;
       servoOffset[ 5] = 299;
       servoOffset[ 6] = 299;
       servoOffset[ 7] = 299;
       servoOffset[ 8] = 299;
       servoOffset[ 9] = 299;
       servoOffset[10] = 299;
       servoOffset[11] = 299;
       servoOffset[12] = 299;
       servoOffset[13] = 299;
       servoOffset[14] = 299;
       servoOffset[15] = 299;
       servoOffset[16] = 299;
       servoOffset[17] = 299;
       servoOffset[18] = 299;
    }
    else    // neither MAC address matched
    {
       nl;
       sp2l("<setupPerBotConfig> Unrecognized MAC address. Per Bot configuration was bypassed", macAdd);
    }
 } // void setupPerBotConfig()
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

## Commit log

2021-08-25 Changed ref from five to six legs
2021-08-25 Added acknowledgement of robot chassis design
2021-08-26 Updated llink to Swampy CAD files
2021-08-27 Fixed spelling of PlatformIO
    [main.h]
2021-08-28 Added acknowledgment for inverser kinematic code
2021-08-28 Added link to assembly instructions
2021-08-28 Added link to assembly instructions.
2021-08-28 Added assembly instruction link.
2021-08-28 Added MD table for leg assembly
2021-08-28 Removed detils about screws
2021-08-29 Updated motor section and added driver details
2021-08-29 Updated assembly link
2021-08-29 Removed leg assembly section
2021-08-29 Added motor picture link
2021-08-29 Added servo horn section
2021-08-29 Added size to motor image
2021-08-29 Reduced size of motor image
2021-08-29 updated servo horn section
2021-08-29 Added all chassis info
2021-08-29 Updated motor driver section
2021-08-29 Fixed wording for upper body plate
2021-08-29 Added link to motor wiring doc
2021-08-29 Fixed URL for wiring motors
2021-08-29 Added wiring motors link
2021-08-30 Added wiring image
2021-08-30 Added wiring chart
2021-08-30 Added pin mappings for Huzzah32 dev board
2021-08-31 Added note that PCB is not ready yet.
2021-09-01 Added logic to handlle bad IP for broker
    [main.cpp]
2021-09-01 Added Adafruit servo PWM library
2021-09-01 Removed I2Cdev library
2021-09-01 In the process of adding I2C communication
2021-09-02 Updated pin usage and descriptions
2021-09-02 Added link to Sparkfun wiring guide
2021-09-02 Fixed formatting of Fritzing diagram insert
2021-09-02 Noted that we are using 30 pin version of dev board
2021-09-02 Added link to circuitry
2021-09-12 Added inverse kinematic model library
2021-09-12 Added I2C bus scanning code
2021-09-12 Added inverse kenetic and wire libraries
2021-09-12 Added inverse kinematic library
2021-09-12 Added servo library
2021-09-12 Added I2c logic. Removed PWM logic.
2021-09-14 Updated servo driver ref. Added status flags.
2021-09-14 Added function to manage servo motors.
2021-09-15 Added menu system using OLED buttons
2021-09-18 Make B screen track leg goal
2021-09-18 Removed all motor control logic.
2021-09-18 Added servo driver status to OLED display
2021-09-18 Track servo driver status
2021-09-18 Added servo driver status
2021-09-23 Added more info about servo motors
2021-09-23 Added diagram of kinematic model
2021-09-23 Added leg logic with kinematic library
2021-09-27 Added IK logic for all 6 legs. Does not work.
    [main.cpp, servo.h]
2021-10-06 Added Arduino log library
2021-10-06 Switch Serial cmmands to Log commands.
2021-10-08 Added TODO comment for issue 23
    [main.cpp]
2021-10-10 Paired down to only Arduino IK function.
2021-10-10 Created this file for generic servo and leg functions.
2021-10-10 Added inlude servoLegs.h file
2021-10-10 Switched serial.print cmds to Log commands.
2021-10-10 Removed include of i2c.h
2021-10-10 Changed ankle joint ref. Added def for positions.
2021-10-10 Converted serial.print to Log commands.
2021-10-22 Track mobility status
2021-10-22 Added RESET button LED definitions.
2021-10-22 Moved servo driver library include to main.h. Fixed bug #29
    [servoLegs.h]
2021-10-22 Added RGB led to robot.
2021-10-26 Removed colour wheel TODO commant.
2021-10-28 Changed huzzah GPIO pin names.
2021-11-19 moved various doc files to repo
    [current-measures.ods, flows-compiler.ods, hex-coord-translation.ods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]
2021-11-22 hex-coord-translation += key locat'n global coords
    [hex-coord-translation.ods]
2021-11-24 added include/flows.h for flows params & storage
    [flows-compiler.ods]
2021-11-30 strat flow implementation
    [hex-coord-translation.ods]
2021-12-01 Implement Flows Assignees: @nerdoug Labels: enhancement Fixes #49
    [flows.cpp, flows.h, mqttBroker.cpp]
2021-12-02 calcs for first flow position now work
2021-12-07 add toe safety checks to avoid dangerous posit'ns
    [flows.cpp, flows.h]
2021-12-08 create an MQTT command to move an arbitrary leg to an arbitrary toe location Fixes #42
    [flows.cpp, flows.h, main.h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]
2021-12-09 Add SSD, SSP and SSO cmds for servo testing - Fixes #59
    [mqttBroker.cpp]
2021-12-10 add hexbot usage in right column
    [pinouts-huzzah.ods]
2021-12-16 remove initial leg moves in initservos
2021-12-29 minor change
    [current-measures.ods, formulas-angles-from-coords.ods]
2022-01-02 avoid servo commands with no position change
    [flows.cpp, flows.h]
2022-01-02 alternate PWM boards in flows
2022-01-05 reduce console message level
    [formulas-angles-from-coords.ods]
2022-01-05 Add LED colours to track flow rows. Fixes #89
    [flows.cpp]
2022-01-13 troubleshoot apparent leg splay
    [debug-angles-2.ods, debug-angles.ods, servo-pwm-movements.ods]
2022-01-13 correct coordsToAngles math
    [formulas-angles-from-coords-b0.ods, formulas-angles-from-coords.ods]
2022-01-13 disable buggy move_leg command
    [mqttBroker.cpp]
2022-01-13 expand MQTT command buffer to hold big flow rows
2022-01-13 geometric tool for calculating flow row coordinates
2022-01-13 more sub-folders in docs
    [current-measures.ods, debug-angles-2.ods, debug-angles.ods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]
2022-01-19 script devel for robot pirouette
    [rotation-global-12degrees.csv, rotation-global-12degrees.ods, rotation-global-12degrees1.csv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]
2022-01-19 fixed MQTT buf size, rotation script work
    [hex-coord-translation.ods]
2022-01-22 see pull/merge comments for change list Fixes #113
    [flows-compiler.ods, hex-coord-translation.ods, rotation-global-12degrees.ods]
2022-01-23 reorg mqtt scripts, +video, trim flows.cpp prints
    [debug-angles-2.ods, debug-angles.ods, rotation-global-12degrees.csv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]
2022-01-23 Document circuit in Frizting tool Fixes #116
    [hexbotBreadboard.fzz]
2022-01-28 Fix wiring diagram Fixes #123
    [hexbotBreadboard.fzz]
2022-01-29 add repeatable cycles: repeat subset of a flow
    [flows-compiler.ods]
2022-01-29 create a script that shows how flow cycles work Fixes #127
2022-01-31 create optional graphable toe position output controlled by FG command at end of script Fixes #129
    [flow-tracker.ods]
2022-02-02 Undo change to Fritzing diagram Fixes #135
    [hexbotBreadboard.fzz]
2022-02-06 create an MQTT script with a walking gait Fixes #133
    [flow-tracker.ods, hex-coord-translation.ods]
2022-02-07 corrections to servo mounting compensation & global> local coord translation
    [flow-tracker.ods]
2022-02-07 fix to servo mounting compensation
    [flows.cpp]
2022-02-09 rename flow_go commands to something more intuitive Fixes #142
    [mqttBroker.cpp]
2022-02-20 add flow command to temporarily redefine the local home coordinates Fixes #143
    [flows.cpp, flows.h, mqttBroker.cpp]
2022-04-09 add 3.3V control for PCA9685s holding issue open
    [flow-tracker.ods]
2022-04-10 add STP command to test servos
2022-04-11 add servo debug code Fixes #164
    [flows.cpp, flows.h]
2022-05-12 Calibrate HS-485HB servos & add software adjustment Fixes #162
    [flows.cpp, flows.h, main.cpp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]
2022-05-15 issue warning if mapDegToPWM() modifies requested angle Fixes #176
    [configDetails.cpp, flows.cpp, flows.h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]
2022-05-19 Update MQTT help command output Fixes #139
    [mqttBroker.cpp]
2022-05-23 Create First Draft GPIO assignments Fixes #179
    [GPIO-pins.ods]
2022-05-24 update Power control diagram Fixes #181
2022-05-24 corrections to doc/circuitry/GPIO-pins.ods Fixes #183
    [GPIO-pins.ods]
2022-05-29 correct comments in GPIO definition source file Fixes #186
    [GPIO-pins.ods]
2022-05-30 adjust power design for 2 pins for 5V Voltage sensing Fixes #187
    [GPIO-pins.ods]
2022-05-30 accumulate datasheets in ..docs/circuitry/datasheets Fixes #190
2022-06-10 create power control scheme using VN7050ASTR MOSFET Fixes #192
    [mosfet1.ods]
2022-06-16 adjust power control circuit Fixes #194
2022-06-20 fix resistor typo in power-test-config.odg Fixes #197
2022-06-22 Add 7050 user manual, fix power drawings Fixes #199
2022-07-03 current dividing documentation Fixes #201
2022-09-25 fixes to power-test-config.odg Fixes #203

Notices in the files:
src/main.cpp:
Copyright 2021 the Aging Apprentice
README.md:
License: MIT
